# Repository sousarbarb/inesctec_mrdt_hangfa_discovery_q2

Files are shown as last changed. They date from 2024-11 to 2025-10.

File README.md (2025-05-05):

# [Integrating Multimodal Perception into Ground Mobile Robots](https://github.com/sousarbarb/inesctec_mrdt_hangfa_discovery_q2)

Repository contains all the documentation associated with the modifications
made by [INESC TEC](https://www.inesctec.pt/en/) on the
[Hangfa Discovery Q2](https://www.hangfa-europe.com/en/omni-robot/discovery)
mobile platform in order to be compatible with multimodal perception. These
modifications also enable the platform to be integrated in the
[Robot Operating System (ROS)](https://ros.org/), facilitating its usage for
research topics such as perception, localisation and mapping, multi-robot
coordination (when more than one platform is available to the user), Artificial
Intelligence (AI) applied on autonomous mobile robotics, among other topics.

## Setup

### Mobile Platform

Check the
[GitHub Pages website](https://sousarbarb.github.io/inesctec_mrdt_hangfa_discovery_q2/)
for more information on the multimodal modifications made to the original
[Hangfa Discovery Q2](https://www.hangfa-europe.com/en/omni-robot/discovery)
mobile platform.

### Firmware

See [README.md](src/firmware/inesctec_mrdt_discovery_q2_fw/README.md) in the
firmware source folder
([src/firmware/inesctec_mrdt_discovery_q2_fw](src/firmware/inesctec_mrdt_discovery_q2_fw/)).

### Robot Operating System (ROS)

- Drivers:
  - [inesctec_mrdt_drivers_interfaces](src/drivers/inesctec_mrdt_drivers_interfaces)
  - [inesctec_mrdt_hangfa_discovery_q2_driver](src/drivers/inesctec_mrdt_hangfa_discovery_q2_driver)
  - [inesctec_mrdt_omnijoy_driver](src/drivers/inesctec_mrdt_omnijoy_driver)
  - [inesctec_mrdt_serial_channels](src/drivers/inesctec_mrdt_serial_channels)
  - [inesctec_mrdt_serial_port](src/drivers/inesctec_mrdt_serial_port)
  - [livox_ros_driver2](src/drivers/livox_ros_driver2)
    _(may be removed from repo to allow further compatibility with ROS versions)_
  - [rslidar_msg](src/drivers/rslidar_msg)
    _(may be removed from repo to allow further compatibility with ROS versions)_
  - [rslidar_sdk](src/drivers/rslidar_sdk)
    _(may be removed from repo to allow further compatibility with ROS versions)_
- Localization:
  [inesctec_mrdt_localization_odom](src/localization/inesctec_mrdt_localization_odom)
- Launch system:
  [inesctec_mrdt_hangfa_discovery_q2_nav_conf](src/inesctec_mrdt_hangfa_discovery_q2_nav_conf)

**ROS supported versions**
- ROS 1
  - [Ubuntu 20.04.6 LTS](https://releases.ubuntu.com/focal/)
  - [ROS Noetic](https://wiki.ros.org/noetic)
- ROS 2
  - [Ubuntu 20.04.6 LTS](https://releases.ubuntu.com/focal/)
  - [ROS 2 Foxy](https://docs.ros.org/en/foxy/)

_Note:_ remove LiDAR specific packages if you want to compile the original
packages developed in the scope of this work on more recent ROS versions.

**Dependencies**
```sh
sudo apt-get install -y libpcap-dev
sudo apt-get install -y ros-$ROS_DISTRO-joy      \
                        ros-$ROS_DISTRO-pcl-ros  \
                        ros-$ROS_DISTRO-libpointmatcher
```

```sh
# Livox-SDK2
git clone https://github.com/Livox-SDK/Livox-SDK2.git
cd Livox-SDK2/
mkdir build
cd build/
cmake .. && make -j
sudo make install
```

```sh
# yaml-cpp
git clone https://github.com/jbeder/yaml-cpp.git
cd yaml-cpp/
mkdir build
cd build/
cmake .. -DYAML_BUILD_SHARED_LIBS=ON && make -j
sudo make install
```

## Usage

### Repository
```sh
git clone git@github.com:sousarbarb/inesctec_mrdt_hangfa_discovery_q2.git --init --recursive
```

### Build
**ROS 1**
```sh
source /opt/ros/$ROS_DISTRO/setup.bash

cd inesctec_mrdt_hangfa_discovery_q2/src
catkin_init_workspace

cd ..
catkin_make --force-cmake --cmake-args -DCMAKE_BUILD_TYPE=Release

source devel/setup.bash
```

**ROS 2**
```sh
source /opt/ros/$ROS_DISTRO/setup.bash

cd inesctec_mrdt_hangfa_discovery_q2
colcon build --cmake-args -DCMAKE_BUILD_TYPE=Release --event-handlers status+ console_direct+ console_start_end+

source install/setup.bash
```

### Launch

**ROS 1**
```sh
# Robot id
export ROBOT_ID=<id>                # (default: unnamed_robot)
# Configuration
export ROBOT_CONF=<configuration>   # (default: basic)

roslaunch inesctec_mrdt_hangfa_discovery_q2_nav_conf wake_up_dumb_q2.launch
```

**ROS 2**
```sh
# Robot id
export ROBOT_ID=<id>                # (default: unnamed_robot)
# Configuration
export ROBOT_CONF=<configuration>   # (default: basic)

ros2 launch inesctec_mrdt_hangfa_discovery_q2_nav_conf wake_up_dumb_q2.launch.xml
```

## Contributing

Any contributions that you make are greatly appreciated. Please proceed as
follows:
1. Fork the repository
2. Create your feature branch
3. Commit your changes
4. Push to the branch in your repository
5. Open a pull request in the project's original repository

## License

Distributed under the _MIT License_.
See [LICENSE](/LICENSE) for more information.

## References

If you use _inesctec_mrdt_hangfa_discovery_q2_ in a work that leads to a
scientific publication, we would appreciate it if you would kindly cite
_inesctec_mrdt_hangfa_discovery_q2_ in your manuscript.

**Plain Text**

R.B. Sousa, H.M. Sobreira, J.G. Martins, P.G. Costa, M.F. Silva and A.P.
Moreira,
"Integrating Multimodal Perception into Ground Mobile Robots,"
_2025 IEEE International Conference on Autonomous Robot Systems and_
_Competitions (ICARSC2025)_, Madeira, Portugal, 2025, pp. 104-111,
doi: [10.1109/ICARSC65809.2025.10970176](https://doi.org/10.1109/ICARSC65809.2025.10970176)
[[github]](https://github.com/sousarbarb/inesctec_mrdt_hangfa_discovery_q2)
[[preprint]](http://doi.org/10.13140/RG.2.2.29381.15845/1)
[[website]](https://sousarbarb.github.io/inesctec_mrdt_hangfa_discovery_q2/)

**BibTex**

```bibtex
@INPROCEEDINGS{sousa2025icarsc,
  author    = {Ricardo B. Sousa and Héber Miguel Sobreira and João G. Martins and Paulo G. Costa and Manuel F. Silva and António P. Moreira},
  booktitle = {2025 IEEE International Conference on Autonomous Robot Systems and Competitions (ICARSC)},
  title     = {Integrating Multimodal Perception into Ground Mobile Robots},
  year      = {2025},
  volume    = {},
  number    = {},
  pages     = {104--111},
  doi       = {10.1109/ICARSC65809.2025.10970176}}
```

## Contacts

If you have any questions or you want to know more about this work, please
contact one of the following contributors:

- Ricardo B. Sousa
  ([rbs@fe.up.pt](mailto:rbs@fe.up.pt))
  _(Corresponding Author)_
  ([github](https://github.com/sousarbarb/),
  [gitlab](https://gitlab.com/sousarbarb/),
  [gitlab](https://gitlab.inesctec.pt/ricardo.b.sousa),
  [orcid](https://orcid.org/0000-0003-4537-5095),
  [google-scholar](https://scholar.google.pt/citations?user=Bz2FMqYAAAAJ),
  [linkedin](https://www.linkedin.com/in/sousa-ricardob/),
  [youtube](https://www.youtube.com/channel/UCXTR8mMlG0VOC_06PKg5KBQ))
- Héber Miguel Sobreira
  ([heber.m.sobreira@inesctec.pt](mailto:heber.m.sobreira@inesctec.pt))
  ([github](https://github.com/HeberSobreira),
  [gitlab](https://gitlab.inesctec.pt/heber.m.sobreira/),
  [orcid](https://orcid.org/0000-0002-8055-1093),
  [google-scholar](https://scholar.google.pt/citations?user=iNhGcpsAAAAJ))
- João G. Martins
  ([joao.g.martins@inesctec.pt](mailto:joao.g.martins@inesctec.pt))
  ([github](https://github.com/Joao-G-Martins),
  [orcid](https://orcid.org/0000-0002-6567-4802))
- Paulo G. Costa
  ([paco@fe.up.pt](mailto:paco@fe.up.pt))
  ([github](https://github.com/P33a),
  [orcid](https://orcid.org/0000-0002-4846-271X),
  [google-scholar](https://scholar.google.pt/citations?user=7Iz8fKcAAAAJ))
- Manuel F. Silva
  ([mss@isep.ipp.pt](mailto:mss@isep.ipp.pt))
  ([orcid](https://orcid.org/0000-0002-0593-2865),
  [google-scholar](https://scholar.google.pt/citations?user=2EFVZ-AAAAAJ))
- António Paulo Moreira
  ([amoreira@fe.up.pt](mailto:amoreira@fe.up.pt))
  ([orcid](https://orcid.org/0000-0001-8573-3147),
  [google-scholar](https://scholar.google.pt/citations?user=eL0gHLoAAAAJ))

## Institutions

- [INESC TEC - Institute for Systems and Computer Engineering, Technology and Science](https://www.inesctec.pt/en/)
- [Faculty of Engineering, University of Porto (FEUP)](https://sigarra.up.pt/feup/en/)

## Acknowledgements

- [5dpo Robotics Team](https://5dpo.github.io/)
- [Amorins & Silva](https://amorinsesilva.pt/)
- [Hangfa Robotics Europe](https://www.hangfa-europe.com/)
- [LattePanda Team](https://www.lattepanda.com/)

## Funding

This work is co-financed by Component 5 - Capitalization and Business
Innovation, integrated in the Resilience Dimension of the Recovery and
Resilience Plan within the scope of the Recovery and Resilience
Mechanism (MRR) of the European Union (EU), framed in the Next Generation EU,
for the period 2021-2026, within project GreenAuto, with reference 54.

**GreenAuto: Green innovation for the Automotive Industry**

- **Operation Code:** 02/C05-i01.02/2022.PC644867037-00000013
- **Beneficiary:** Peugeot Citröen Automóveis Portugal, S.A.
- **Work Package:** WP10 - Automated logistics for the automotive industry
- **Product, Processes, or Services (PPS):**
  PPS18 - 3D navigation system for mobile robotic equipment
- **Consortium Partners:**
    - [Flowbotic Mobile Systems, Lda](https://www.flowbotic.eu/) _(leader)_
    - [Faculty of Engineering, University of Porto (FEUP)](https://www.up.pt/feup/en/)
    - [INESC TEC - Institute for Systems and Computer Engineering, Technology and Science](https://www.inesctec.pt/en/)
    - [STAR](https://starinstitute.pt/)
    - [Kaizen](https://kaizen.com/pt-pt/)
    - [Institute for Systems and Robotics (ISR)-Coimbra](https://www.isr.uc.pt/)
- **Timeline:** October 2021 - December 2025
- **Duration:** 51 months
- **URL:**
  [https://transparencia.gov.pt/en/fundos-europeus/prr/beneficiarios-projetos/projeto/02/C05-i01.02/2022.PC644867037-00000013/](https://transparencia.gov.pt/en/fundos-europeus/prr/beneficiarios-projetos/projeto/02/C05-i01.02/2022.PC644867037-00000013/)

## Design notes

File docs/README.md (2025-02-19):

# GitHub Pages

Public page of the repository based on GitHub actions through the template
**Material** (https://squidfunk.github.io/mkdocs-material/) from **MkDocs**
(https://www.mkdocs.org/) Markdown-based static site
generation.

## Setup

### GitHub Repository

```sh
mkdir ~/dev
cd ~/dev

git clone git@github.com:sousarbarb/inesctec_mrdt_hangfa_discovery_q2.git
```

### Material for MkDocs

```sh
pip install mkdocs-material
```

## Usage

### Local

```sh
cd ~/dev/inesctec_mrdt_hangfa_discovery_q2

mkdocs serve -a <localhost IP 127.0.0.1>:<PORT>
```

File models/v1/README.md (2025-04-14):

# 3D Models of the Revised Hangfa Discovery Q2 Platform

This folder presents all the 3D models designed for the revised platform in
[AutoDesk Fusion 360](https://www.autodesk.com/products/fusion-360/).
These models include a simplified 3D model for the mechanical platform,
a STEP+F3D file for each 3D-printed PETG component considered in the
revision, as well as a major F3D file that aglomerates all models into a single
project:
- **[hangfa-discovery-q2_mechanical-platform.f3d](hangfa-discovery-q2_mechanical-platform.f3d):**
  original mechanical platform of the
  [Hangfa Discovery Q2](https://www.hangfa-europe.com/en/omni-robot/discovery)
  omnidirectional mobile robot
- **[hangfa-discovery-q2_multimodal-perception-mechanical-integration.f3d](hangfa-discovery-q2_multimodal-perception-mechanical-integration.f3d):**
  major [AutoDesk Fusion 360](https://www.autodesk.com/products/fusion-360/)
  project that aglomerates all 3D models design in the scope of this work into a
  single project file
- **electronics_baseplate\*.\*:** framework to host all the electronics proposed
  in the paper inside the metallic box of the original
  [Hangfa Discovery Q2](https://www.hangfa-europe.com/en/omni-robot/discovery)
  platform
- **battery_xiaomi-powerbank-50W-20000mAh_case\*.\*:** case for the
  Powerbank Xiaomi Mi 50W 20000mAh
- **hangfa-discovery-q2_optitrack_\*.\*:** OptiTrack 3D-printed accessories to
  fixate onto the robot (wheels and top bend metal sheet) in order to track the
  platform's pose with the OptiTrack Motion Capture (MoCap) system
  (compatible with IR-reflective tracking spheres from OptiTrack on M4 screws)
- **sbc_lattepanda-3-delta_case\*.\*:** case for the
  [LattePanda 3 Delta](https://www.lattepanda.com/lattepanda-3-delta)
  Single Board Computer (SBC)
- **sensors-plate_front-support_rgbd-cameras\*.\*:** generic RGBD cameras
  model (see the compatibility further down) as the front support of the top
  bend metal sheet
- **sensors-plate_back-support_wi-fi-antennas\*.\*:** Wi-Fi antennas model as
  the back support of the top bend metal sheet (should increase wireless network
  connectivity)
- **sensors-plate_\<sensor type\>_\<sensor model\>\*.\*:** 3D-printed supports
  to fixate the `<sensor model>` to the top bend metal sheet

Even though the repository is focused on the v1 version of the overhaul revision
of the platform, there was an initial version ([v0](/models/v0/)) that only
focused on adding a 2D laser scanner and no Single Board Computer (SBC). Indeed,
in that version, we assumed the user would use a laptop for testing the
platform.

## 3D Models

### Front Support for RGBD Cameras

**Requirements**

- Intel RealSense D455/455f/456 (M4, 95mm distance between
  two screws horizontal direction,
  _[intel dev](https://dev.intelrealsense.com/docs/intel-realsense-d400-series-product-family-datasheet)_)
- Intel RealSense L515 (M3, 40mm distance between two screws vertical direction,
  _[intel dev](https://dev.intelrealsense.com/docs/lidar-camera-l515-datasheet)_)
- OAK-D and OAD-D Pro Series (M4, 75mm distance between
  two screws horizontal direction - compatibility with VESA mouting holes,
  _[depthai-hardware](https://github.com/luxonis/depthai-hardware)_)

### Generic Support for 3D LiDARs

**Requirements**

- Livox Mid-360 (M3, 65x65mm, 36x48mm rectangular hole pattern,
  _[mid-360 user manual](https://www.livoxtech.com/mid-360/downloads)_)
- Ouster
  |                          | Holes | Dimensions | Distance between Screws | Description | Source |
  | ------------------------ | :---: | :--------: | :---------------------: | ----------- | :----: |
  | OS0 Rev7 w/ Baseplate    | M8    | 110x110mm  | 80mm | square hole pattern | (_[ouster dev](https://static.ouster.dev/sensor-docs/hw_user_manual/hw_common_sections_OS0/os0-overview.html)_) |
  | OS1 Rev7 w/ Baseplate    | M8    | 110x110mm  | 80mm | square hole pattern | (_[ouster dev](https://static.ouster.dev/sensor-docs/hw_user_manual_OS1/hw_common_sections_OS1/os1-overview.html)_) |
  | OSDome Rev7 w/ Baseplate | M8    | 110x110mm  | 80mm | square hole pattern | (_[ouster dev](https://static.ouster.dev/sensor-docs/hw_user_manual_OSDome/hw_common_sections_OSDome/osdome-overview.html)_) |
- RoboSense Helios Series (M3, 99.8mm diameter, 90mm diameter with a triangular hole pattern
  _[helios series user guide](https://www.robosense.ai/en/resources-81)_)
- Velodyne Puck Series / VLP (1/4''-20, 103mm diameter,
  1 center screw with 2x M4 alignment features separated by 88.9mm,
  _[velodyne puck/vlp](https://ouster.com/downloads/velodyne-downloads)_)

## Gallery

**Revised Hangfa Discovery Q2 Platform**

Front-Left Perspective View

Front-Right Perspective View

Front View

Right View

Back View

Left View

**Perspective Views from AutoDesk Fusion 360 on the Revised Platform** _(but still orthographic projection...)_

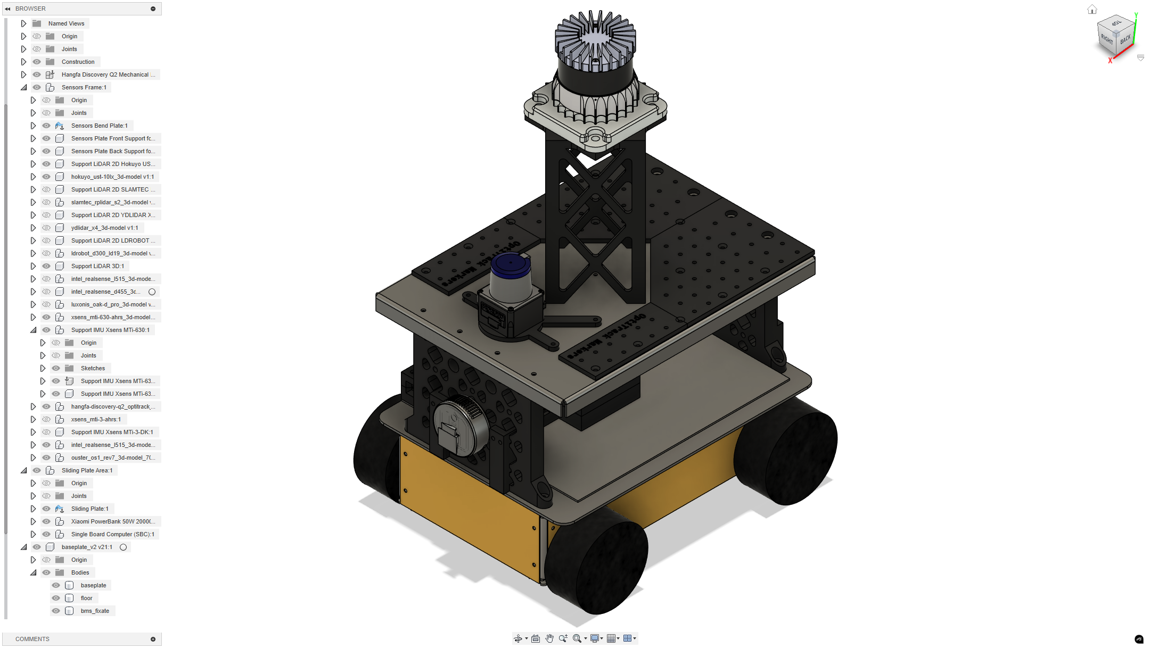
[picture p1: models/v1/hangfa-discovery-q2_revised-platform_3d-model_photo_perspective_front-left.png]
Front-Left Perspective View


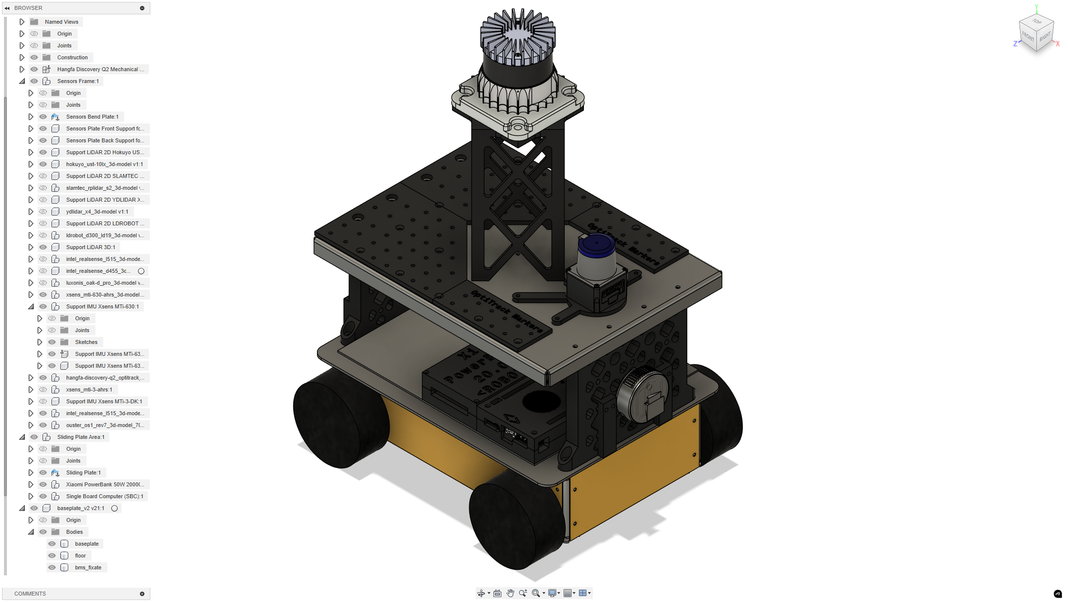
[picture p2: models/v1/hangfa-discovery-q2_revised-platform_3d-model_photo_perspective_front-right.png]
Front-Right Perspective View


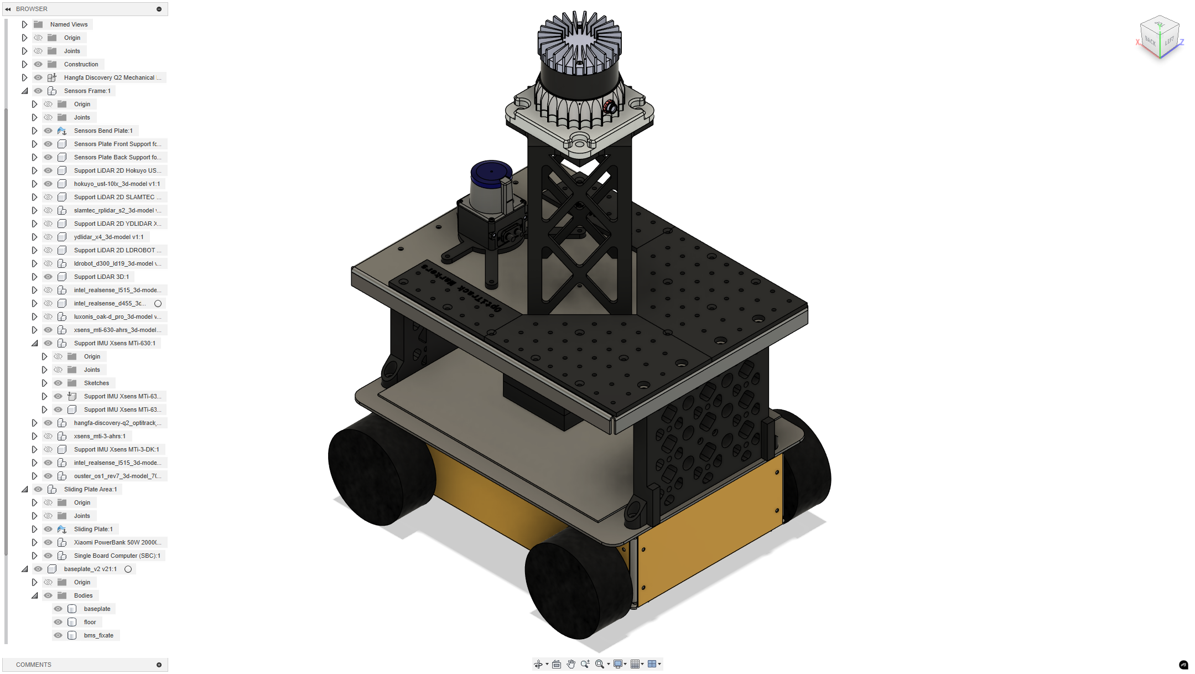
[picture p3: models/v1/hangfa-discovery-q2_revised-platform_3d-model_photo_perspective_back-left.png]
Back-Left Perspective View


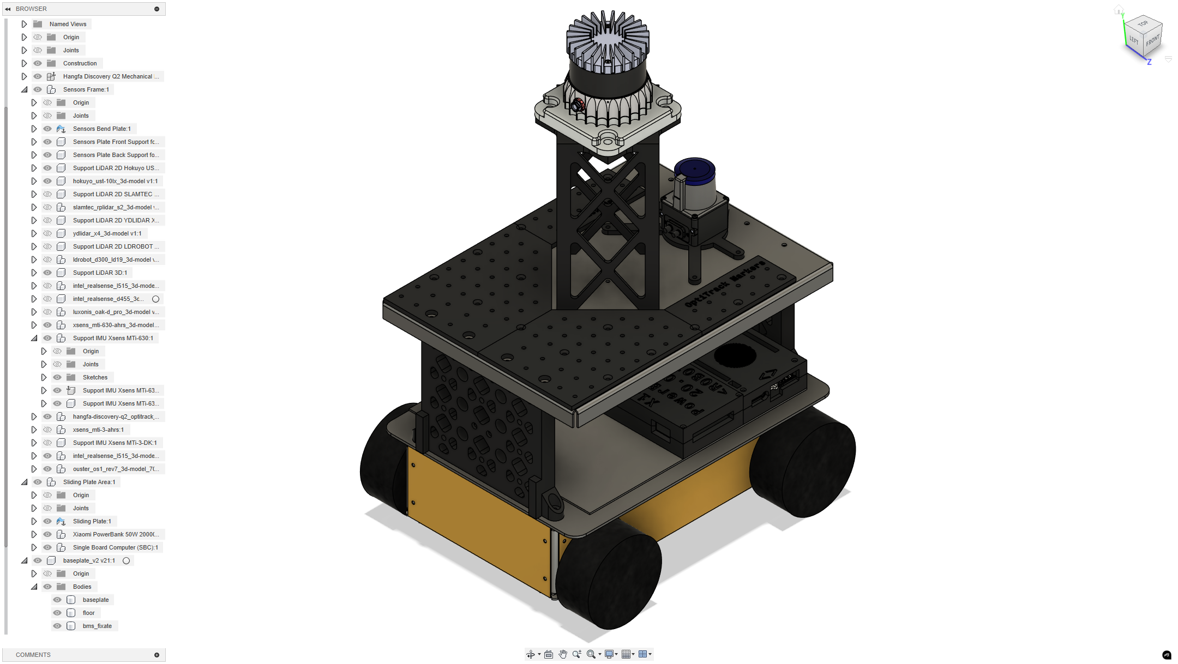
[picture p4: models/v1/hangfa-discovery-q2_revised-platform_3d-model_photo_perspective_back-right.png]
Back-Right Perspective View


**Ortographic Views from AutoDesk Fusion 360 on the Revised Platform**

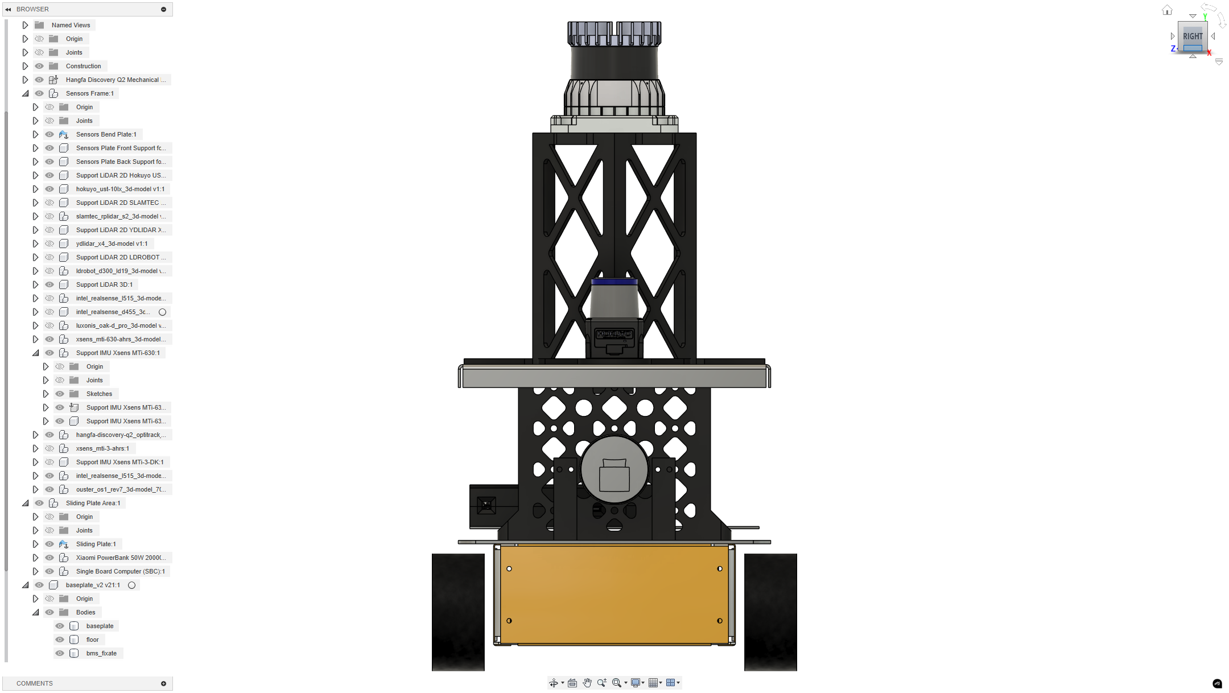
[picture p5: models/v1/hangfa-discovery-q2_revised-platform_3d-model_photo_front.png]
Front Ortographic View


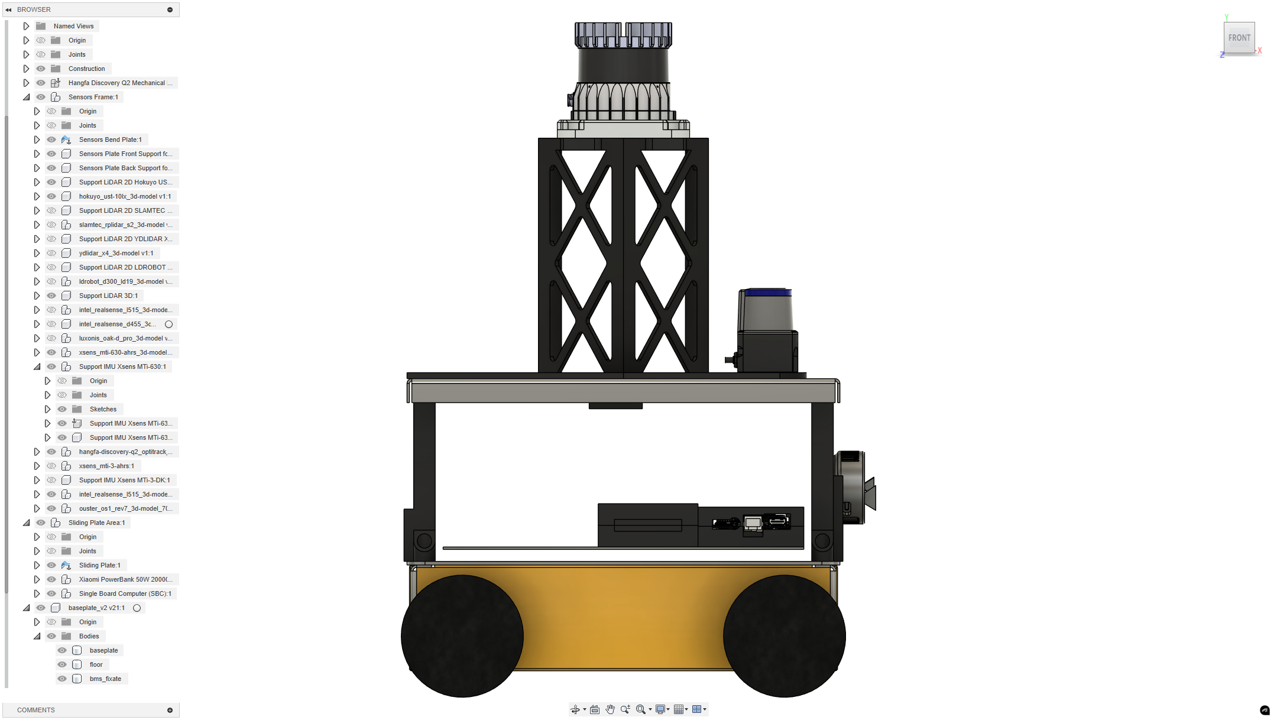
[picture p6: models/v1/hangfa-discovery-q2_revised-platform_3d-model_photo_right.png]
Right Ortographic View


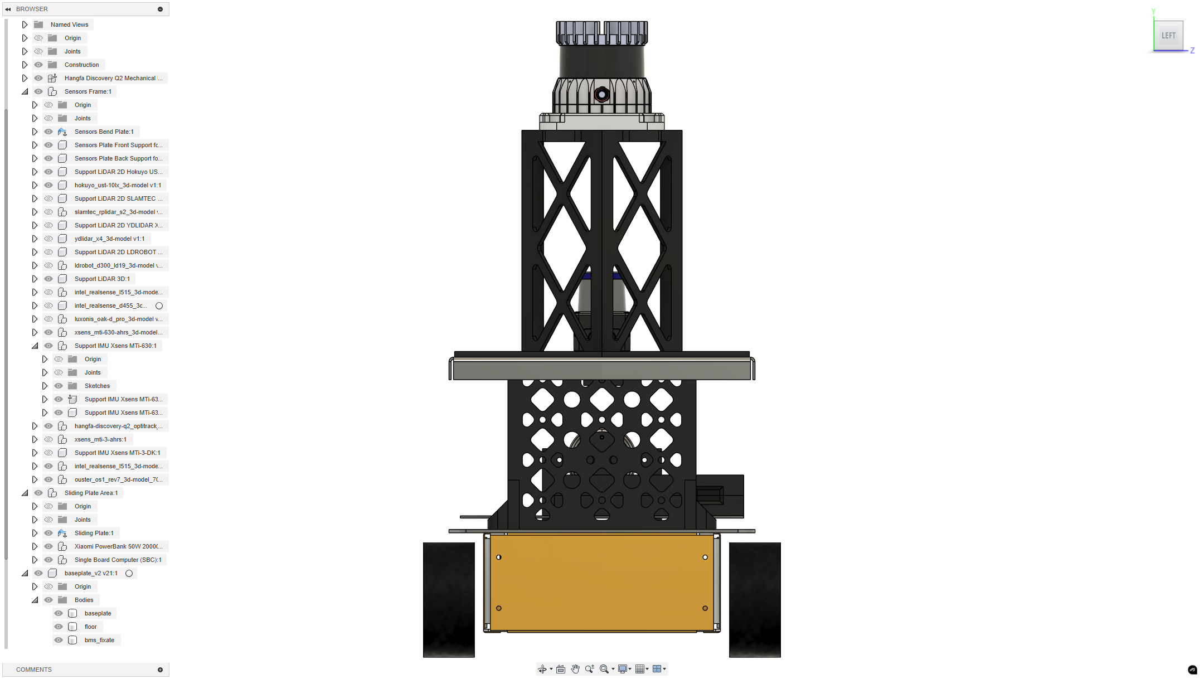
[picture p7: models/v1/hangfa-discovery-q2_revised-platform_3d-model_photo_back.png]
Back Ortographic View


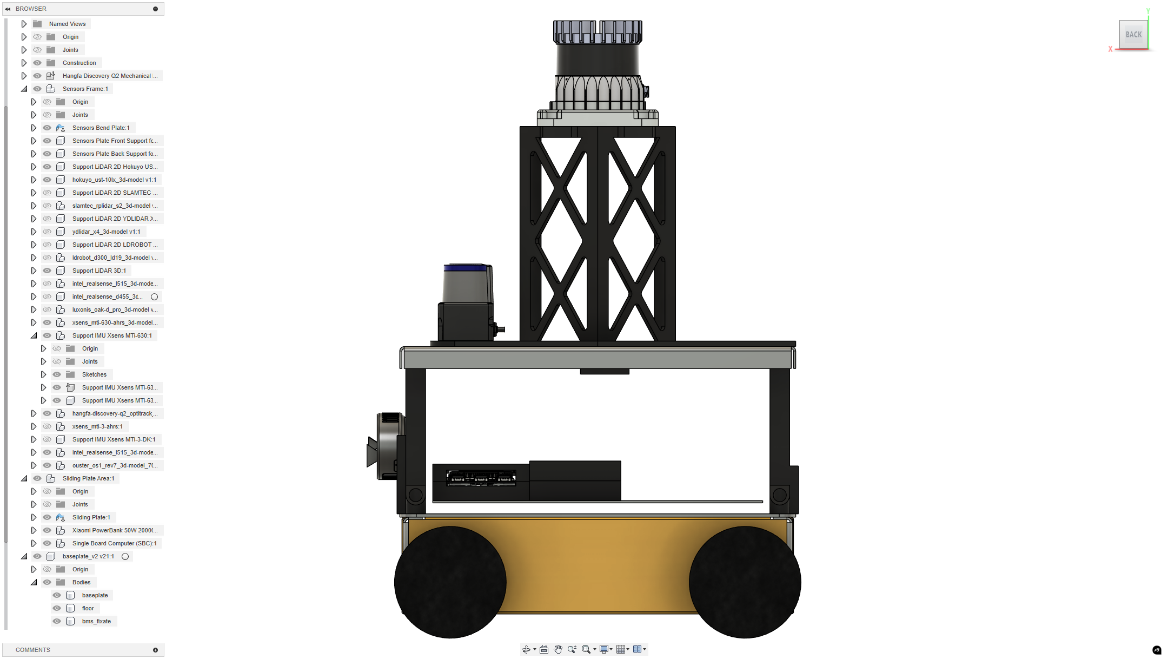
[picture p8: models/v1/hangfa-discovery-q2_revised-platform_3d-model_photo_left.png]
Left Ortographic View


**Miscellaneous...**

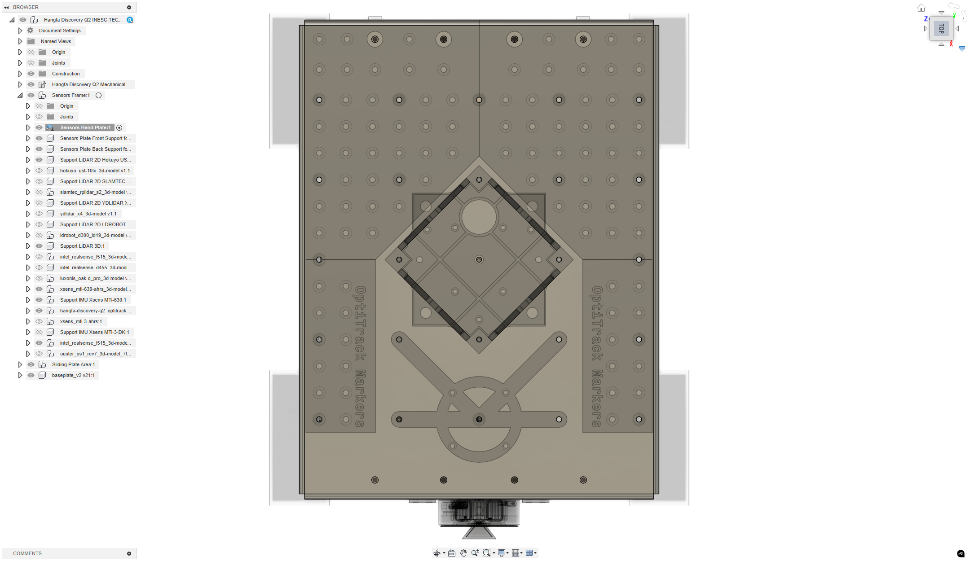
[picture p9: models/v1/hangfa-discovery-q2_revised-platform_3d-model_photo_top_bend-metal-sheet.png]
Bend metal sheet to house 2D/3D sensors


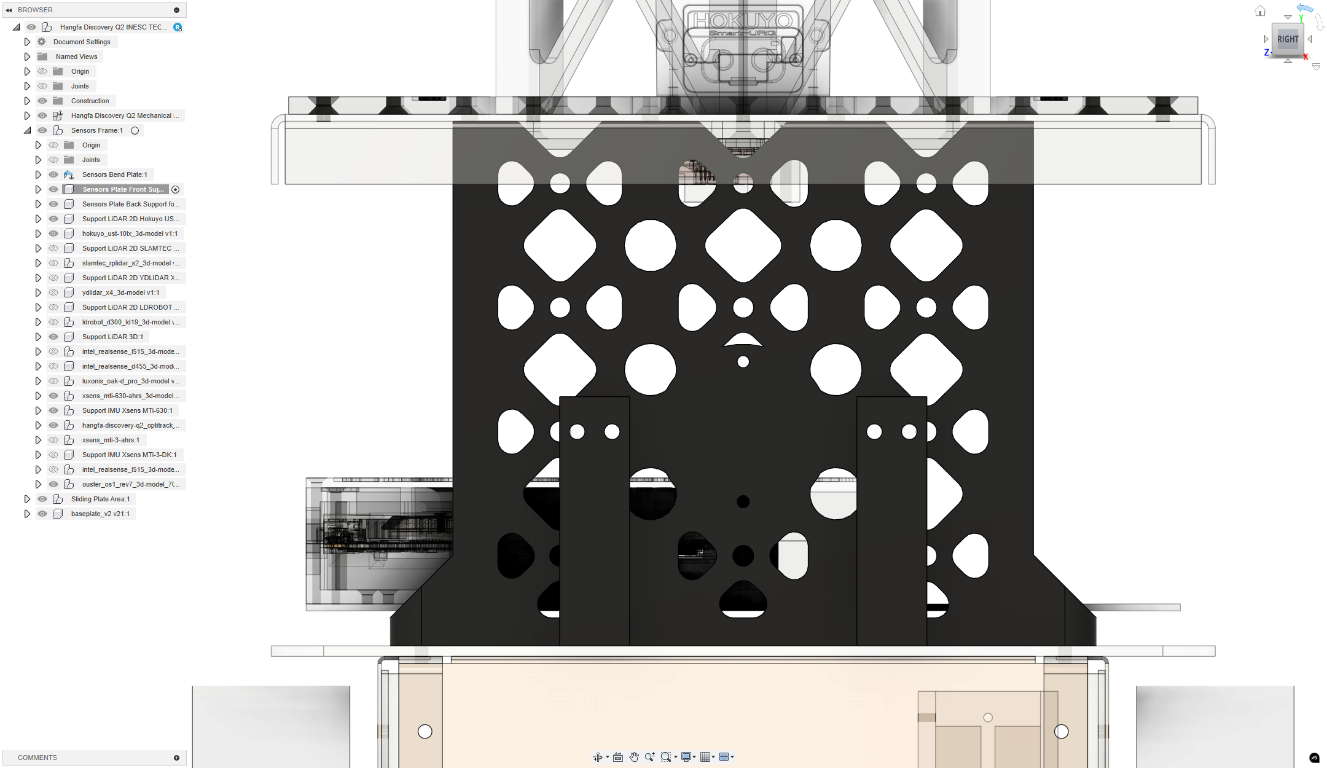
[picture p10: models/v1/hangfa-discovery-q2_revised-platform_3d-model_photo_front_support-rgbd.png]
Front support of the bend metal sheet for RGBD cameras


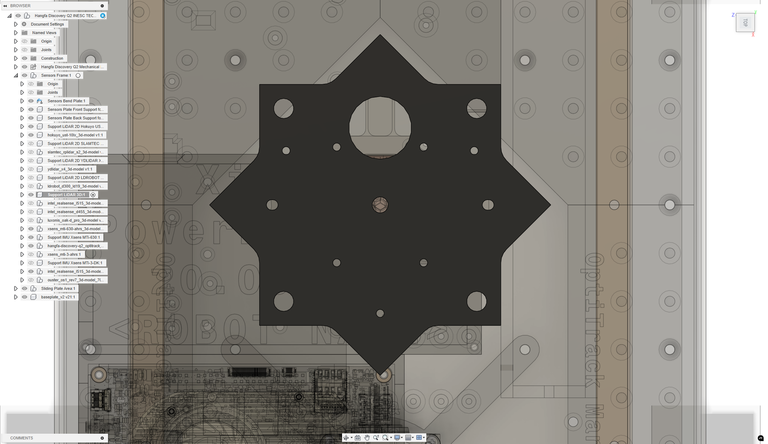
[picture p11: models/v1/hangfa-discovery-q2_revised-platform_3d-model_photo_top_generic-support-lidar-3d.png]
Generic support to fixate on top of the bend metal sheet for 3D LiDARs


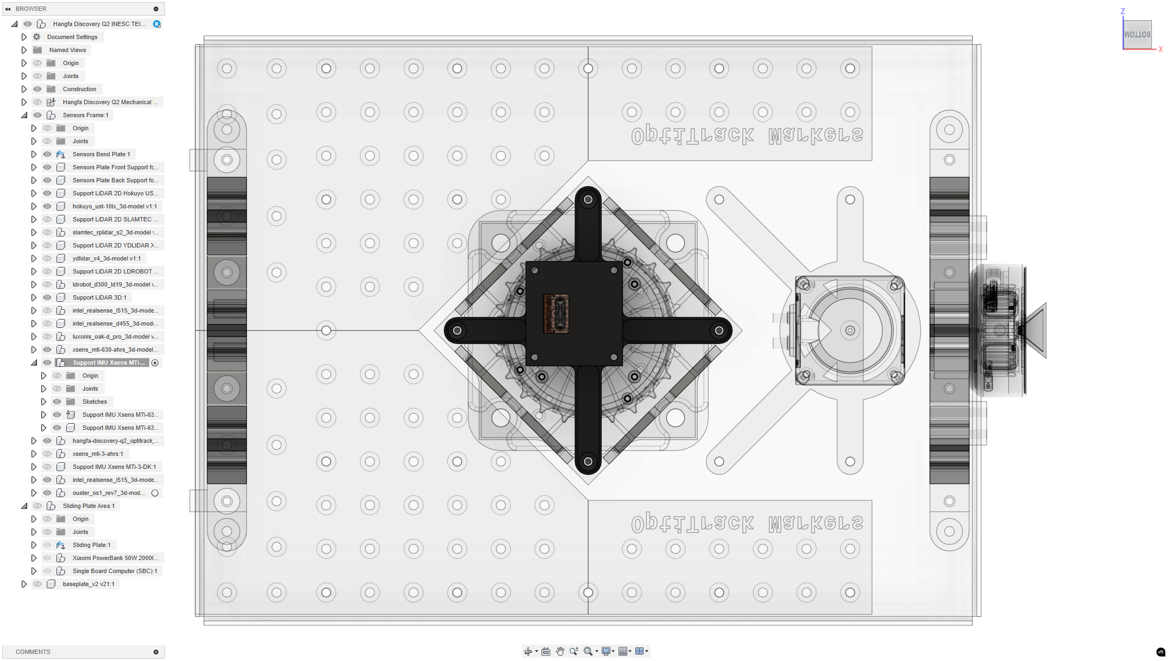
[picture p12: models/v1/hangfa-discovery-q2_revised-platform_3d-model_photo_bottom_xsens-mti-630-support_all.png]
Xsens MTi-630 AHRS support on the bottom of the bend metal sheet - all components visible


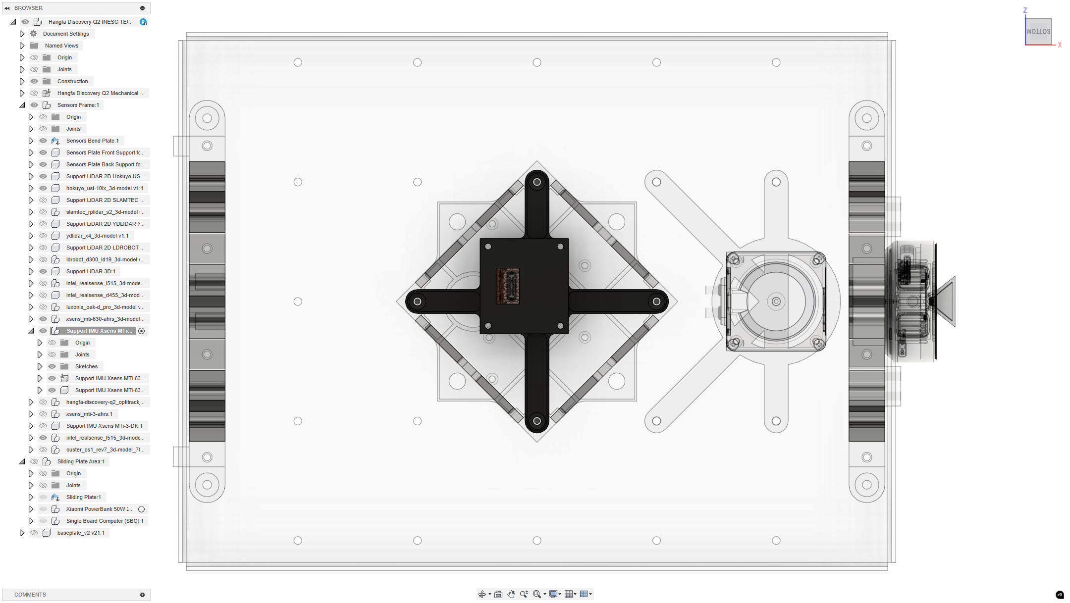
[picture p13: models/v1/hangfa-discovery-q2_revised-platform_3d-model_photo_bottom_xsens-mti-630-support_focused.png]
Xsens MTi-630 AHRS support on the bottom of the bend metal sheet - focused


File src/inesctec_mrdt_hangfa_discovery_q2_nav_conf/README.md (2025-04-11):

# inesctec_mrdt_hangfa_discovery_q2_nav_conf

This repository implements the launch files required to operate the
[Hangfa Discovery Q2](http://www.hangfa.com/EN/robot/DiscoveryQ2.html)
four-wheeled omnidirectional robot, one of the "twin" yellow robots.
The system implemented is based on the INESC TEC Robotics Navigation Stack that
it allows you to have different configurations implemented and selecting just
one based on your environment variables.

**Version 0.3.0**

**With this version, it is possible to do:**

- Basic environment configuration (firmware driver, joystick, wheeled odometry)
- Basic 2D laser scanner configuration (basic + laser 2D) w/ Hokuyo UST-10LX
- Basic 3D LiDAR configuration (basic + lidar 3D) w/ Livox Mid-360

**The next version will add these features:**

- TBD

## Environment Configurations

- `basic`
  - drivers
    - inesctec_mrdt_hangfa_discovery_q2_driver
    - inesctec_mrdt_omnijoy_driver_logif710
  - hmi
    - rviz
  - localization
    - inesctec_mrdt_localization_odom
- `basic_2d`
  - drivers
    - inesctec_mrdt_hangfa_discovery_q2_driver
    - inesctec_mrdt_omnijoy_driver_logif710
    - static_transform_publisher (laser > base_footprint)
    - urg_node
  - hmi
    - rviz
  - localization
    - inesctec_mrdt_localization_odom
  - **Additional configurations:**
    - Network:
      1. Open the Settings > Network
      2. Select the _Hokuyo_ wired interface settings
- `basic_3d`
  - drivers
    - livox_ros_driver2
    - inesctec_mrdt_hangfa_discovery_q2_driver
    - inesctec_mrdt_omnijoy_driver_logif710
    - static_transform_publisher (lidar3d > base_footprint)
  - hmi
    - rviz
  - localization
    - inesctec_mrdt_localization_odom
  - **Additional configurations:**
    - Network:
      1. Open the Settings > Network
      2. Select the _Livox Mid-360_ / _RoboSense Helios_ wired interface
         settings

## ROS

**ROS 1**

- [Ubuntu 20.04.6 LTS](https://releases.ubuntu.com/focal/)
- [ROS Noetic](https://wiki.ros.org/noetic)

**ROS 2**

- [Ubuntu 20.04.6 LTS](https://releases.ubuntu.com/focal/)
- [ROS 2 Foxy](https://docs.ros.org/en/foxy/)

## Usage

### Setup

```sh
# Robot id
export ROBOT_ID=<id>                # (default: unnamed_robot)
# Configuration
export ROBOT_CONF=<configuration>   # (default: basic)
```

### Compilation

**ROS 1**

```sh
# ROS 1 environment setup
source /opt/ros/noetic/setup.bash

# Clone the repository
git clone git@github.com:sousarbarb/inesctec_mrdt_hangfa_discovery_q2.git

# ROS 1 workspace setup
cd inesctec_mrdt_hangfa_discovery_q2/src
catkin_init_workspace

# Build
cd ..
catkin_make --force-cmake -DCMAKE_BUILD_TYPE=Release
# OR catkin_make_isolated (more slow, build and check dependencies individually)
# OR catkin build (requires the Pyhton-based catkin tools)
source devel/setup.bash
```

**ROS 2**

```sh
# ROS 2 environment setup
source /opt/ros/foxy/setup.bash

# Clone the repository
git clone git@github.com:sousarbarb/inesctec_mrdt_hangfa_discovery_q2.git

# Build
cd inesctec_mrdt_hangfa_discovery_q2
colcon build --cmake-args -DCMAKE_BUILD_TYPE=Release --event-handlers summary+ status+ console_cohesion+ console_direct+ console_start_end+ console_stderr+
source install/setup.bash
```

### Launch

**ROS 1**

```sh
roslaunch inesctec_mrdt_hangfa_discovery_q2_nav_conf wake_up_dumb_q2.launch
```

**ROS 2**

```sh
ros2 launch inesctec_mrdt_hangfa_discovery_q2_nav_conf wake_up_dumb_q2.launch.xml
```

## Acknowledgements

- [5dpo Robotics Team](https://5dpo.github.io/)
- [Faculty of Engineering, University of Porto (FEUP)](https://sigarra.up.pt/feup/en/)
- [INESC TEC - Institute for Systems and Computer Engineering, Technology and Science](https://www.inesctec.pt/en/)

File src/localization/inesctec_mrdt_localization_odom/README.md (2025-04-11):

# inesctec_mrdt_localization_odom

This repository implements a data processor for the estimation of the robot pose
based on odometric-only data (e.g., wheeled, laser, visual, and/or inertial
odometry). The ROS package implemented in this repository makes available nodes
that may leverage one and/or multiple sources of odometry data for dead
reckoning pose estimation of the robot.

**Version 1.4.0**

**With this version, it is possible to do:**

- Wheeled odometry (four-wheeled omnidirectional steering geometry)
- Wheeled odometry (differential and three-wheeled omnidirectional steering
  geometries)
- Inverse wheeled odometry
- Enable/disable publication of the tf base_frame_id > odom_frame_id
- Limit the maximum angular speed of the wheels and scale the velocities

**The next version will add these features:**

- Wheeled odometry (tricycle steering geometry)
- Fusion of wheels and inertial odometry data
- Dynamic reconfigure of the nodes parameters
- Additional parameter for covariance (wheeled-inertial odometry fusion)

## ROS

**ROS 1**

- [Ubuntu 20.04.6 LTS](https://releases.ubuntu.com/focal/)
- [ROS Noetic](https://wiki.ros.org/noetic)

**ROS 2**

- [Ubuntu 20.04.6 LTS](https://releases.ubuntu.com/focal/)
- [ROS 2 Foxy](https://docs.ros.org/en/foxy/)

### Dependencies

- [rclcpp](https://index.ros.org/r/rclcpp/) (_ROS 2_)
- [roscpp](https://wiki.ros.org/roscpp/) (_ROS 1_)
- [geometry_msgs](https://index.ros.org/p/geometry_msgs/)
- [nav_msgs](https://index.ros.org/p/nav_msgs/)
- inesctec_mrdt_drivers_interfaces
- [tf2](https://index.ros.org/p/tf2/)
- [tf2_ros](https://index.ros.org/p/tf2_ros/)

### Parameters

- base_frame_id (`std::string = "base_footprint"`): tf frame id of the robot
  base footprint coordinate frame
- odom_frame_id (`std::string = "odom"`): tf frame id of the robot odometry
  coordinate frame
- publish_tf (`bool = true`): enable the publication of the tf
  base_frame_id > odom_frame_id
- invert_tf (`bool = false`): enable the invertion of the tf (odom_frame_id >
  base_frame_id instead of base_frame_id > odom_frame_id)
- w_ref_max_enabled (`bool = false`): enable a maximum angular speed for the
  robot wheels
- w_ref_max (`double`): maximum angular speed of the robot wheels
- steering_geometry: steering geometry of the mobile robot (rad/s)
  (`"diff" | "tricyc" | "omni3" | "omni4"`)
  - Differential drive
    - rob_dist_between_wh (`double`): distance between left-right wheels (m)
    - wh_right_diam (`double`): right wheel diameter (m)
    - wh_right_idx (`size_t`): right wheel index in the
      [mot_enc_array.msg](https://github.com/5dpo/5dpo_ros_interfaces/blob/main/5dpo_ros_interfaces_hw/msg/mot_enc_array.msg)
      (0..1)
    - wh_right_inv (`bool`): invert positive direction of the right
      wheel angular motion
    - wh_left_diam (`double`): left wheel diameter (m)
    - wh_left_idx (`size_t`): left wheel index in the
      [mot_enc_array.msg](https://github.com/5dpo/5dpo_ros_interfaces/blob/main/5dpo_ros_interfaces_hw/msg/mot_enc_array.msg)
      (0..1)
    - wh_left_inv (`bool`): invert positive direction of the left
      wheel angular motion
  - Tricycle
    - TBD
  - Three-wheeled omnidirectional robot
    - rob_dist_center_wh (`double`): distance between the robot geometric center
      and the omnidirectional wheels (m)
    - wh_front_right_diam (`double`): front-right wheel diameter (m)
    - wh_front_right_idx (`size_t`): front-right wheel index in the
      [mot_enc_array.msg](https://github.com/5dpo/5dpo_ros_interfaces/blob/main/5dpo_ros_interfaces_hw/msg/mot_enc_array.msg)
      (0..2)
    - wh_front_right_inv (`bool`): invert positive direction of the front-right
      wheel angular motion
    - wh_front_left_diam (`double`): front-left wheel diameter (m)
    - wh_front_left_idx (`size_t`): front-left wheel index in the
      [mot_enc_array.msg](https://github.com/5dpo/5dpo_ros_interfaces/blob/main/5dpo_ros_interfaces_hw/msg/mot_enc_array.msg)
      (0..2)
    - wh_front_left_inv (`bool`): invert positive direction of the front-left
      wheel angular motion
    - wh_back_diam (`double`): back wheel diameter (m)
    - wh_back_idx (`size_t`): back wheel index in the
      [mot_enc_array.msg](https://github.com/5dpo/5dpo_ros_interfaces/blob/main/5dpo_ros_interfaces_hw/msg/mot_enc_array.msg)
      (0..2)
    - wh_back_inv (`bool`): invert positive direction of the back
      wheel angular motion
  - Four-wheeled omnidirectional robot
    - rob_dist_between_front_back_wh (`double`): distance between front-back
      wheels (m)
    - rob_dist_between_left_right_wh (`double`): distance between left-right
      wheels (m)
    - wh_front_left_diam (`double`): front-left wheel diameter (m)
    - wh_front_left_idx (`size_t`): front-left wheel index in the
      [mot_enc_array.msg](https://github.com/5dpo/5dpo_ros_interfaces/blob/main/5dpo_ros_interfaces_hw/msg/mot_enc_array.msg)
      (0..3)
    - wh_front_left_inv (`bool`): invert positive direction of the front-left
      wheel angular motion
    - wh_front_right_diam (`double`): front-right wheel diameter (m)
    - wh_front_right_idx (`size_t`): front-right wheel index in the
      [mot_enc_array.msg](https://github.com/5dpo/5dpo_ros_interfaces/blob/main/5dpo_ros_interfaces_hw/msg/mot_enc_array.msg)
      (0..3)
    - wh_front_right_inv (`bool`): invert positive direction of the front-right
      wheel angular motion
    - wh_back_left_diam (`double`): back-left wheel diameter (m)
    - wh_back_left_idx (`size_t`): back-left wheel index in the
      [mot_enc_array.msg](https://github.com/5dpo/5dpo_ros_interfaces/blob/main/5dpo_ros_interfaces_hw/msg/mot_enc_array.msg)
      (0..3)
    - wh_back_left_inv (`bool`): invert positive direction of the back-left
      wheel angular motion
    - wh_back_right_diam (`double`): back-right wheel diameter (m)
    - wh_back_right_idx (`size_t`): back-right wheel index in the
      [mot_enc_array.msg](https://github.com/5dpo/5dpo_ros_interfaces/blob/main/5dpo_ros_interfaces_hw/msg/mot_enc_array.msg)
      (0..3)
    - wh_back_right_inv (`bool`): invert positive direction of the back-right
      wheel angular motion

### Subscribes

- cmd_vel (`geometry_msgs::Twist.msg`)
- motors_enc (`inesctec_mrdt_drivers_interfaces::MotEncArray.msg`)

### Publishes

- cmd_vel_ref (`geometry_msgs::Twist.msg`)
- motors_ref (`inesctec_mrdt_drivers_interfaces::MotRefArray.msg`)
- odom (`nav_msgs::Odometry.msg`)
- tf2 (N/A)
  - base_frame_id > odom_frame_id

### Services

None.

### Actions

None.

## Usage

### Compilation

**ROS 1**

```sh
# ROS 1 environment setup
source /opt/ros/noetic/setup.bash

# Clone the repository
git clone git@github.com:sousarbarb/inesctec_mrdt_hangfa_discovery_q2.git

# ROS 1 workspace setup
cd inesctec_mrdt_hangfa_discovery_q2/src
catkin_init_workspace

# Build
cd ..
catkin_make --force-cmake -DCMAKE_BUILD_TYPE=Release
# OR catkin_make_isolated (more slow, build and check dependencies individually)
# OR catkin build (requires the Pyhton-based catkin tools)
source devel/setup.bash
```

**ROS 2**

```sh
# ROS 2 environment setup
source /opt/ros/foxy/setup.bash

# Clone the repository
git clone git@github.com:sousarbarb/inesctec_mrdt_hangfa_discovery_q2.git

# Build
cd inesctec_mrdt_hangfa_discovery_q2
colcon build --cmake-args -DCMAKE_BUILD_TYPE=Release --event-handlers summary+ status+ console_cohesion+ console_direct+ console_start_end+ console_stderr+
source install/setup.bash
```

### Launch

**ROS 1**

```sh
roslaunch inesctec_mrdt_localization_odom inesctec_mrdt_localization_odom_wh.launch
```

**ROS 2**

```sh
ros2 launch inesctec_mrdt_localization_odom inesctec_mrdt_localization_odom_wh.launch.xml
```

## Acknowledgements

- [5dpo Robotics Team](https://5dpo.github.io/)
- [Faculty of Engineering, University of Porto (FEUP)](https://sigarra.up.pt/feup/en/)
- [INESC TEC - Institute for Systems and Computer Engineering, Technology and Science](https://www.inesctec.pt/en/)

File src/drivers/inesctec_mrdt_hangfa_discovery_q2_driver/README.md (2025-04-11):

# inesctec_mrdt_hangfa_discovery_q2_driver

**Version 2.1.1**

This repository implements a driver within a ROS package to communicate with the
firmware present in the Hangfa Q2 Discovery robot. The driver is required
for communicating with the robot and have available all its different functions.

The serial communication is handled by
[Boost.Asio](https://www.boost.org/doc/libs/1_80_0/doc/html/boost_asio.html).
This communication is based on the example `4_callback` provided in the
[serial-port](https://github.com/fedetft/serial-port) GitHub repository.

**With this version, it is possible to do:**

- Communicate with Arduino Mega 2560 using Boost.Asio
  (inesctec_mrdt_serial_port)
- Subscribe motors angular speed reference
- Publish encoders data (encoders + wheels angular speed)
- Read encoders
- Set motors speed
- Reset driver upon reset signal
- Watchdog timer to monitor the motors angular speed reference
- Send serial message to the firmware upon reconnection of the serial port
  communication
- Check automatically (1Hz) the status of the serial port communication

**The next version will add these features:**

No further development is expected for this package.

## ROS

**ROS 1**

- [Ubuntu 20.04.6 LTS](https://releases.ubuntu.com/focal/)
- [ROS Noetic](https://wiki.ros.org/noetic)

**ROS 2**

- [Ubuntu 20.04.6 LTS](https://releases.ubuntu.com/focal/)
- [ROS 2 Foxy](https://docs.ros.org/en/foxy/)

### Dependencies

- [rclcpp](https://index.ros.org/r/rclcpp/) (_ROS 2_)
- [roscpp](https://wiki.ros.org/roscpp/) (_ROS 1_)
- inesctec_mrdt_drivers_interfaces
- inesctec_mrdt_serial_port
- inesctec_mrdt_serial_channels

### Parameters

- encoder_res (`float = 48.0`): resolution of the encoder (ticks/rot)
- gear_reduction (`float = 64.0`): reduction ratio of the transmissions
  (\[gear_reduction:1\])
- serial_port_name (`std::string = "/dev/ttyACM0"`): name of the serial port

### Subscribes

- motors_ref (`inesctec_mrdt_drivers_interfaces::MotRefArray.msg`)

### Publishes

- motors_enc (`inesctec_mrdt_drivers_interfaces::MotEncArray.msg`)

### Services

None.

### Actions

None.

## Usage

### Compilation

**ROS 1**

```sh
# ROS 1 environment setup
source /opt/ros/noetic/setup.bash

# Clone the repository
git clone git@github.com:sousarbarb/inesctec_mrdt_hangfa_discovery_q2.git

# ROS 1 workspace setup
cd inesctec_mrdt_hangfa_discovery_q2/src
catkin_init_workspace

# Build
cd ..
catkin_make --force-cmake -DCMAKE_BUILD_TYPE=Release
# OR catkin_make_isolated (more slow, build and check dependencies individually)
# OR catkin build (requires the Pyhton-based catkin tools)
source devel/setup.bash
```

**ROS 2**

```sh
# ROS 2 environment setup
source /opt/ros/foxy/setup.bash

# Clone the repository
git clone git@github.com:sousarbarb/inesctec_mrdt_hangfa_discovery_q2.git

# Build
cd inesctec_mrdt_hangfa_discovery_q2
colcon build --cmake-args -DCMAKE_BUILD_TYPE=Release --event-handlers summary+ status+ console_cohesion+ console_direct+ console_start_end+ console_stderr+
source install/setup.bash
```

### Launch

**ROS 1**

```sh
roslaunch inesctec_mrdt_hangfa_discovery_q2_driver inesctec_mrdt_hangfa_discovery_q2_driver.launch
```

**ROS 2**

```sh
ros2 launch inesctec_mrdt_hangfa_discovery_q2_driver inesctec_mrdt_hangfa_discovery_q2_driver.launch.xml
```

## Acknowledgements

- [5dpo Robotics Team](https://5dpo.github.io/)
- [Faculty of Engineering, University of Porto (FEUP)](https://sigarra.up.pt/feup/en/)
- [INESC TEC - Institute for Systems and Computer Engineering, Technology and Science](https://www.inesctec.pt/en/)

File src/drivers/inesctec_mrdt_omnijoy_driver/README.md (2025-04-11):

# inesctec_mrdt_omnijoy_driver

**Version 0.1.0**

This repository implements a ROS driver to control an omnidirectional robot
(but also compatible with other steering geometries) with a joystick controller.

**With this version, it is possible to do:**

- Joystick control of a mobile robot
- Dynamic reconfigure of the node parameters

**The next version will add these features:**

No further development is foreseen for this package.

## ROS

**ROS 1**

- [Ubuntu 20.04.6 LTS](https://releases.ubuntu.com/focal/)
- [ROS Noetic](https://wiki.ros.org/noetic)

**ROS 2**

- [Ubuntu 20.04.6 LTS](https://releases.ubuntu.com/focal/)
- [ROS 2 Foxy](https://docs.ros.org/en/foxy/)

### Dependencies

- [rclcpp](https://index.ros.org/r/rclcpp/) (_ROS 2_)
- [roscpp](https://wiki.ros.org/roscpp/) (_ROS 1_)
- [dynamic_reconfigure](https://index.ros.org/p/dynamic_reconfigure/) (_ROS 1_)
- [geometry_msgs](https://index.ros.org/p/geometry_msgs/)
- [joy](https://index.ros.org/p/joy/)
- [sensor_msgs](https://index.ros.org/p/sensor_msgs/)

### Parameters

- axis_linear_x (`int = 1`): index number of x linear axis (`/joy.axes`)
- axis_linear_y (`int = 2`): index number of y linear axis (`/joy.axes`)
- axis_angular (`int = 0`): index number of angular axis (`/joy.axes`)
- axis_deadman (`int = 4`): index number of button for deadman switch
  (`/joy.buttons`)
- axis_turbo (`int = 5`): index number of button for turbo (`/joy.buttons`)
- axis_turbo_up (`int = 6`): index number of button for increasing boost
  (`/joy.buttons`)
- axis_turbo_down (`int = 7`): index number of button for decreasing boost
  (`/joy.buttons`)
- scale_linear (`double = 0.1`): linear scale to normalize (m/s)
- scale_angular (`double = 0.2`): angular scale to normalize (rad/s)
- turbo_scale_linear (`double = 0.2`): use this scale instead of `scale_linear`
  when pressing the turbo button (m/s)
- turbo_max_scale_linear (`double = 0.4`): maximum linear turbo scale (m/s)
- turbo_scale_angular (`double = 0.4`): use this scale instead of
  `scale_angular` when pressing the turbo button (rad/s)
- turbo_max_scale_angular (`double = 0.8`): maximum angular turbo scale (rad/s)

In order to know the index numbers of your controller, go to
[joy](https://wiki.ros.org/joy) documentation, _5. Application_, to see the
options available for those parameters.

### Subscribes

- joy (`sensor_msgs::Joy.msg`)

### Publishes

- cmd_vel (`geometry_msgs::Twist.msg`)

### Services

None.

### Actions

None.

## Usage

### Compilation

**ROS 1**

```sh
# ROS 1 environment setup
source /opt/ros/noetic/setup.bash

# Clone the repository
git clone git@github.com:sousarbarb/inesctec_mrdt_hangfa_discovery_q2.git

# ROS 1 workspace setup
cd inesctec_mrdt_hangfa_discovery_q2/src
catkin_init_workspace

# Build
cd ..
catkin_make --force-cmake -DCMAKE_BUILD_TYPE=Release
# OR catkin_make_isolated (more slow, build and check dependencies individually)
# OR catkin build (requires the Pyhton-based catkin tools)
source devel/setup.bash
```

**ROS 2**

```sh
# ROS 2 environment setup
source /opt/ros/foxy/setup.bash

# Clone the repository
git clone git@github.com:sousarbarb/inesctec_mrdt_hangfa_discovery_q2.git

# Build
cd inesctec_mrdt_hangfa_discovery_q2
colcon build --cmake-args -DCMAKE_BUILD_TYPE=Release --event-handlers summary+ status+ console_cohesion+ console_direct+ console_start_end+ console_stderr+
source install/setup.bash
```

### Launch

**ROS 1**

```sh
roslaunch inesctec_mrdt_omnijoy_driver inesctec_mrdt_omnijoy_driver_logif710.launch
```

**ROS 2**

```sh
ros2 launch inesctec_mrdt_omnijoy_driver inesctec_mrdt_omnijoy_driver_logif710.launch.xml
```

## Acknowledgements

- [@fedetft](https://github.com/fedetft)
- [5dpo Robotics Team](https://5dpo.github.io/)
- [Faculty of Engineering, University of Porto (FEUP)](https://sigarra.up.pt/feup/en/)
- [INESC TEC - Institute for Systems and Computer Engineering, Technology and Science](https://www.inesctec.pt/en/)

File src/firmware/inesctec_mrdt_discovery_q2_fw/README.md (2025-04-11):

# inesctec_mrdt_discovery_q2_fw

This repository implements the firmware relative to the modified
Hangfa Discovery Q2 four-wheeled omnidirectional robotic platform.

**Version 2.2.0**

**With this version, it is possible to do:**

- Serial communication using the library channels
- Read encoders channel A and B for wheeled odometry
- Motors angular speed control with a generic PID controller
- Motors PWM control
  ([TimerOne](https://github.com/PaulStoffregen/TimerOne) and
  [TimerThree](https://github.com/PaulStoffregen/TimerThree) PWM)
- Watchdog timer to disable the motors if the PC does not send anything for a
  certain time
- Limitation on the PWM change

**The next version will add these features:**

- Tune the PID controllers for angular speed control of the motors

**Bugs identified in the current version:**

- None

## Hardware

- Hangfa Discovery Q2 Platform
- Faulhaber DC Motor 2342 OEM
  ([datasheet [not possible to validate this link...]](https://www.faulhaber.com/fileadmin/Import/Media/EN_2342_CR_DFF.pdf))
  - 3K3 Ohms Resistors (pull-up resistor for the encoders channels)
- Arduino Mega 2560 Rev3
- Arduino Mega Proto Shield Rev3
  - IDC Socket 6Way
    ([store](https://mauser.pt/catalog/product_info.php?products_id=011-0827))
  - IDC Header Straight 6Way
    ([store](https://mauser.pt/catalog/product_info.php?products_id=011-0800))
  - 8-pin stackable header (Arduino Compatible)
    ([store](https://opencircuit.nl/product/female-header-stackable-8-pin-10-stuks))
  - 10-pin stackable header (Arduino Compatible)
    ([store](https://opencircuit.nl/product/female-header-stackable-10-pin-10-stuks))
  - 2x18-pin stackable header (Arduino Compatible)
    ([store](https://opencircuit.nl/product/female-header-stackable-2x18-pin-2-stuks))
- Cytron 13A, 5-30V Single DC Motor Controller
  - KK shell connector 3Way 2.54mm (Molex 5051 Housing)
    ([store](https://mauser.pt/catalog/product_info.php?products_id=011-1319))
  - Terminals KK shell connector 3Way 2.54mm
    ([store](https://mauser.pt/catalog/product_info.php?products_id=011-3065))
- Li-Ion 18650 BMS Charger PCB, 3S 12.6V 20A
- Tattu 11.1V 15C 3S 10000mAh Lipo Battery Pack

## Serial Communication (channels)

**Robot > PC**

- `[g]`: encoders total count of motor 0 (ticks)
- `[h]`: encoders total count of motor 1 (ticks)
- `[i]`: encoders total count of motor 2 (ticks)
- `[j]`: encoders total count of motor 3 (ticks)
- `[k]`: interval time between control cycles (us)
- `[r]`: reset signal

**PC > Robot**

- `[G]`: reference angular speed of motor 0 (rad/s)
- `[H]`: reference angular speed of motor 1 (rad/s)
- `[I]`: reference angular speed of motor 2 (rad/s)
- `[J]`: reference angular speed of motor 3 (rad/s)
- `[K]`: PWM value of motors
  - `(value >> 24) & 0x03`: motor index (0..3)
  - `value & 0xFFFF`: PWM value (0..`kMotPWMmax`)

## Usage

**Requirements**

- PlatformIO extension for VS Code

### Compilation

**Visual Studio Code**

1. Clone the repository
    ```sh
    git clone git@github.com:sousarbarb/inesctec_mrdt_hangfa_discovery_q2.git
    cd inesctec_mrdt_hangfa_discovery_q2/src/firmware/inesctec_mrdt_discovery_q2_fw
    code .
    ```
2. Compile the project using the PlatformIO extension in VS Code
   (PlatformIO on left-side navigation bar > Project Tasks > Build)

### Run

1. Open the PlatformIO project in the Visual Studio Code
2. Upload the project using the PlatformIO extension in VS Code
   (PlatformIO on left-side navigation bar > Project Tasks > Upload)

## Acknowledgements

- [5dpo Robotics Team](https://5dpo.github.io/)
- [Faculty of Engineering, University of Porto (FEUP)](https://sigarra.up.pt/feup/en/)
- [INESC TEC - Institute for Systems and Computer Engineering, Technology and Science](https://www.inesctec.pt/en/)

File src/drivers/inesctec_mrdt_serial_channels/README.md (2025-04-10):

# inesctec_mrdt_serial_channels

**Version 1.0**

This folder contains a ROS package that defines a library to communicate with
another devices such as Arduinos (Uno, Mega, etc). The communication protocol is
based on the _channels_ library developed by professor Paulo Costa. The current
version is an improvement over the one developed by Héber Miguel Sobreira
(https://gitlab.inesctec.pt/heber.m.sobreira/serial_communication_channels.git)
in the way that allows channels between 'g'-'z' and 'G'-'Z'. An important note
is that you must check if on the Arduino side the hexdecimals characters
correspond to the ones consider in this package: '0'..'9','A'..'F'.

Lastly, it is possible to use the same library on the Arduino (example provided
by Héber Miguel Sobreira - please contact him through email
[heber.m.sobreira@inesctec.pt](mailto:heber.m.sobreira@inesctec.pt)
for further informations on this matter).
However, this implementation uses reallocs of memory. Even though it is only
when the Arduino turns on, I did not think that this approach would be the
correct one due to Arduinos do not have a proper memory management system. So,
the one used on the Arduino is the same one developed by professor Paulo Costa.
**Main disadvantage:** the Arduino only interprets fixed-size packets
(specifically, 4 bytes of data: `float`, `uint32_t` or `int32_t`).

**With this version, it is possible to:**

- Send data of the following types: `float`, `uint32_t` or `int32_t`
  (limited because of the implementation on the Arduino side)
- 40 different channels with different functions associated with each one
  ('g'-'z' and 'G'-'Z')

**The next version will add these features:**

- Binary write and read (compression that allows to reduce from 8 to 4 bytes of
  data on certain data types)

## ROS

**ROS 1**

- [Ubuntu 20.04.6 LTS](https://releases.ubuntu.com/focal/)
- [ROS Noetic](https://wiki.ros.org/noetic)

**ROS 2**

- [Ubuntu 20.04.6 LTS](https://releases.ubuntu.com/focal/)
- [ROS 2 Foxy](https://docs.ros.org/en/foxy/)

## Communication Protocol

- `[CHANNEL]` + `[DATA]` + `\0`
- `[CHANNEL]`: 'g'-'z', 'G'-'Z'
- `[DATA]`: characters that represent a value in hexadecimal

## Acknowledgements

- [5dpo Robotics Team](https://5dpo.github.io/)
- [Faculty of Engineering, University of Porto (FEUP)](https://sigarra.up.pt/feup/en/)
- [INESC TEC - Institute for Systems and Computer Engineering, Technology and Science](https://www.inesctec.pt/en/)
- [Héber Miguel Sobreira](https://gitlab.inesctec.pt/heber.m.sobreira/)
- [Paulo G. Costa](https://github.com/P33a)

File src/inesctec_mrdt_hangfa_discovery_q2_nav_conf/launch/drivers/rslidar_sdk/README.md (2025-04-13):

# [RoboSense RS-Helios 5515](https://www.robosense.ai/en/rslidar/RS-Helios)

## Specifications

| Description | Specification |
| :--- | :---: |
| #beams | 32 |
| Blind spot | 0.2m |
| Frame rate | 10 / 20Hz |
| Rotation speed | 600rpm @ 10Hz, 1200rpm @ 20Hz |
| HFOV | 360º |
| VFOV | 70º (-55º..+15º) |
| Horizontal resolution | 0.2º @ 10Hz, 0.4º @ 20Hz |
| Vertical resolution | up to 1.33º (not uniform) |
| Operating Voltage | 9..32V |
| Power consumption | 12W (typical), 20W (peak) |

## Setup

1. Power up the sensor
2. Connect an Ethernet cable to your PC
3. Configure a local network:
   - Manual
   - Address: 192.168.1.102
   - Netmask: 255.255.255.0
4. Validate the sensor configuration with the web browser: http://192.168.1.200/
   - **Return Mode:** due to beam divergence, multiple laser returns may appear
     from any single laser shot
     - Strongest
     - Last
     - First
     - Dual: details enhance, twice the volume of data versus single return mode
       - Sensor records both returns only when distance between two objects is
         greater than 1m
   - **Phase Lock:** when multiple lasers are used at the same time, with a PPS
     pulse signal; indicates the firing angle of the sensor's laser at the time
     of the rising edge of the PPS signal
   - **Reflectivity Enhance:** noise filter

## ROS

### Version

- ROS1
- ROS2

### Setup

**foxy**

1. Install a ROS 2 full desktop version
2. Download and install dependencies
   ```sh
   sudo apt-get install -y  libpcap-dev
   ```
3. Clone and configure the SDK repository
   (https://github.com/RoboSense-LiDAR/rslidar_sdk)
   ```sh
   # ROS 2
   source /opt/ros/foxy/setup.bash
   mkdir -p ~/ros2_ws/src
   cd ~/ros2_ws/src

   git clone git@github.com:sousarbarb/rslidar_sdk.git
   git clone git@github.com:sousarbarb/rslidar_msg.git

   cd rslidar_sdk
   git submodule init
   git submodule update --recursive

   cp package_ros2.xml package.xml
   nano CMakeLists.txt    # change CATKIN to COLCON

   # Build
   cd ~/ros2_ws
   colcon build
   source install/setup.bash
   ```
   - **Note:** a fork was made from the original SDK to support putting the
     config file in another folder

### Launch

```sh
roslaunch inesctec_mrdt_hangfa_discovery_q2_nav_conf run_rslidar_sdk.launch.xml
```

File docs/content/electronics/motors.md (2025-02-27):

# Motors

| Description | Value |
| :--- | :---: |
| Model | Faulhaber 2342 OEM DC motor |
| Voltage (Rated) | 12V |
| Current (Rated) | 1.1A |
| Output Power (Rated) | 11W |
| Speed (Rated) | 5800rpm |
| Speed (No-load) | 6800rpm |
| Encoders | 5V, 2 channels, 12CPR |
| Fixation Type | outer body bearing block bears the wheel in axial and radial loads |

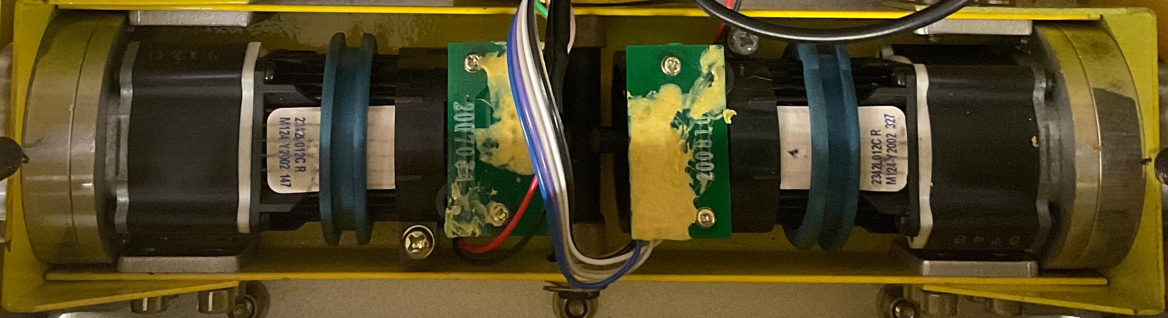
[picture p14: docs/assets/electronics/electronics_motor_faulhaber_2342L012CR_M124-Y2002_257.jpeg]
Faulhaber 2342 OEM DC motor on Discovery Q2 Platform


## Drivers

- **Goal:** control the DC motors of the original
  [Hangfa Discovery Q2](https://www.hangfa-europe.com/en/omni-robot/discovery)
  mobile platform
- **Model:** Cytron 13A 5-30V Single DC Motor Driver
- Voltage range 5-30V compatible with the Faulhaber 2342 OEM DC motor (12V)
- Maximum continuous current of 13A and peak motor current of 30A should be
  compatible with the Faulhaber 2342 OEM DC motor (rated at 1.1A, 11W)
- Single PWM signal for speed control with a digital direction pin to set the
  direction of the motor speed
- 3.3V and 5V logic level input compatible with the Arduino Mega 2560
  microcontroller

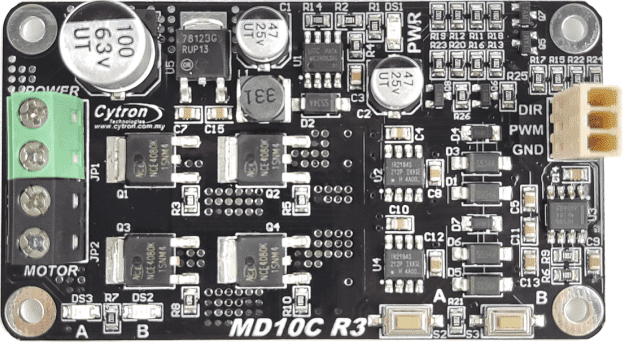
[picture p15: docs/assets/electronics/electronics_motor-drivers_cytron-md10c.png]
Cytron 13A 5-30V Single DC Motor Driver


## Encoders

- **Goal:** 5V, 2 channels, 12CPR encoders present on the Faulhaber 2342 OEM DC
  motors (green PCB board on top of the motors) generate quadrature signals for
  the microcontroller to read the angular speed of the motors
- **Requirement:** upon experimental test, 3.3 kΩ pull-up resistors are soldered
  to the channels A and B inputs of the four encoders on the microcontroller's
  proto shield to reduce signal noise and improve the quadrature between
  channels A and B

!!! Warning

    The cables on the encoders of the original
    [Hangfa Discovery Q2](https://www.hangfa-europe.com/en/omni-robot/discovery)
    mobile platform seem to not be correctly soldered into the encorder's green
    board. This flaw may lead to incorrect encoders reading. As a result, you
    probably are more safe if you resolder all the cables in the encoders.

!!! Tip

    The yellow stuff on the encoder's green board comes out with heat (e.g., use
    a heat gun carefully with the help of a tool to remove the yellow stuff in
    order to be able to resolder the cables).

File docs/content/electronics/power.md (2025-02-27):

# Power

## Battery

- **Goal:** power all the electronics related to the robot's base platform
  (including motors, motor drivers, external devices of the user that may
  require DC power)
- **Model:** Tattu 10000mAh 11.1V 15C 3S LiPo Battery
- 11.1V makes it compatible to power the Faulhaber 2342 OEM DC motors (12V)
- 11.1V is also compatible to power the Arduino Mega 2560 (7-12V recommended,
  6-20V limit), even though the microcontroller can be powered directly from the
  USB connection

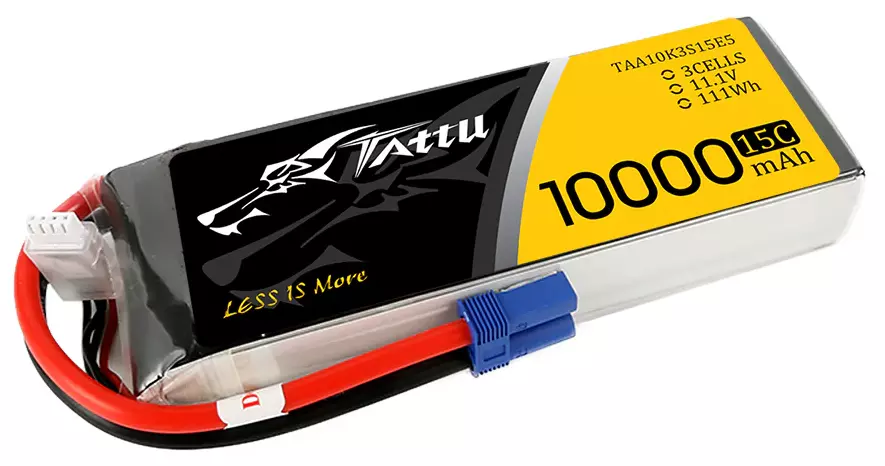
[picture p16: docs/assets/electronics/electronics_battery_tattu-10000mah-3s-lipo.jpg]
Tattu 10000mAh 11.1V 15C 3S LiPo Battery


## Battery Management System (BMS)

- **Goal:** balance the voltage of the battery cells both when discharging and
  upon charging
- **Model:** 18650 BMS Charger 3S 12.6V 20A Rev. 2.0
- Compatible with 3S (three cells in series) batteries
- Compatible with the maximum voltage of each LiPo cell (4.2V)

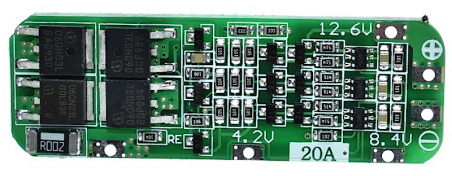
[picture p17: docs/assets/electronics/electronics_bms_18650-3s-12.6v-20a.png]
18650 BMS Charger 3S 12.6V 20A Rev. 2.0


## DC/DC Buck-Boost Converter

- **Goal:** provide a regulated and adjustable DC power output for external
  devices (e.g., Ethernet switch, 3D LiDARs)
- **Model:** DC 5-30V to 1.25-30V 8A Buck Boost Converter
- Input voltage compatible with the output voltage of the LiPo battery
- Output voltage compatible with common voltage values such as 5V / 12V / 24V

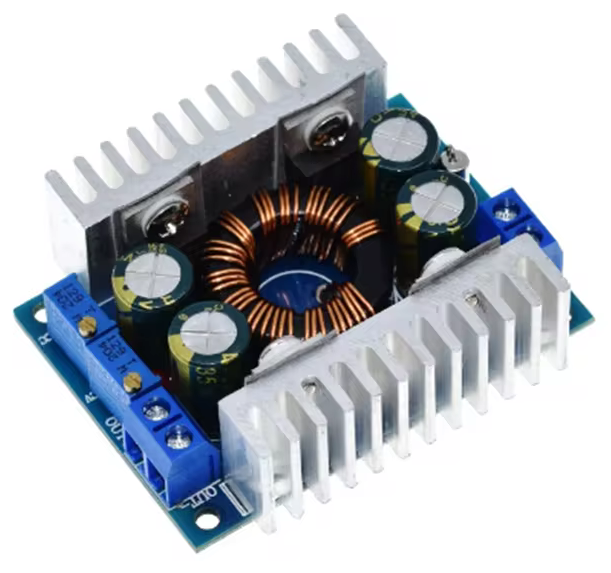
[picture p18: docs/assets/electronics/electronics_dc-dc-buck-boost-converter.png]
DC 5-30V to 1.25-30V 8A Buck Boost Converter


## Charging

**Hangfa Discovery Q2**

- **A:** charging connector
- **B:** 20A power fuse for electrical protection
- **C:** ON/OFF switch

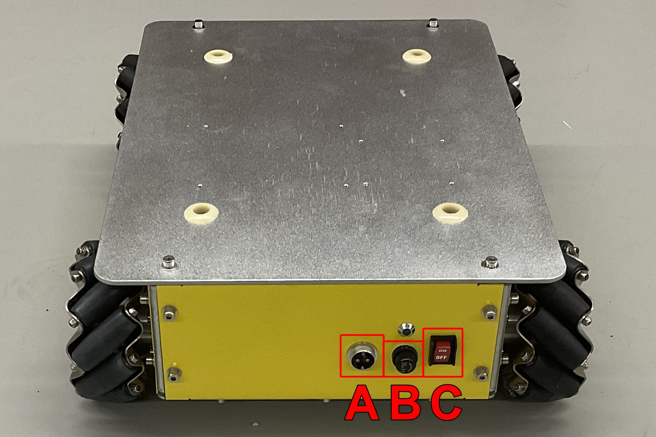
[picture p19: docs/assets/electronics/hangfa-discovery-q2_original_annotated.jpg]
Front View of the Hangfa Discovery Q2 Platform


### Original Charger

**Model:** KXD-126300 Li-ion charger, 100~240VAC input, 12.6VDC @ 3.0A output

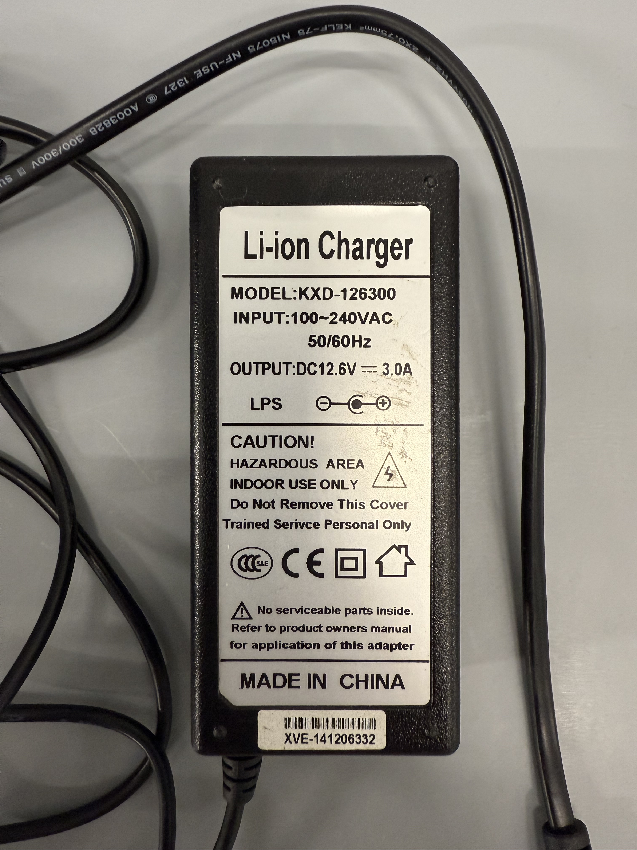
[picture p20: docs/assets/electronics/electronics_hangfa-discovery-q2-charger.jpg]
KXD-126300 Li-ion charger, 100~240VAC input, 12.6VDC @ 3.0A output


!!! Warning

    The original charger that comes with the platform may not be the
    most suitable for charging the LiPo battery. Even if the charger
    indicator turns green, it does not necessarily mean that charging
    has stopped, which could lead to overcharging and potentially
    swollen batteries.

1. Turn OFF the Discovery Q2 platform
2. Connect the charger to AC power (LED on the charger should turn green)
3. Connect the charger output plug to the Discovery Q2 platform
    - If the LED on the charger turns red, it is charging the platform
    - Otherwise, the battery is fully charged
4. Disconnect the charger from the platform when the battery is fully charged

### LiPo Charger

- **Model:** LiPo Battery Charger LBC-011 (or any other charger specific for
  LiPo batteries)
    - [iMAX B6AC User Manual](../../assets/electronics/battery-charger_imaxb6ac_user-manual.pdf)

LiPo Battery Charger LBC-011

1. Turn OFF the Discovery Q2 platform
2. Connect the charger to AC power (charger screen should turn on)
3. Select the **CHARGE** mode (use the buttons
   **:octicons-triangle-left-24: Status :octicons-triangle-right-24:** to
   navigate through the available modes)
4. If the charger is not configure for **LiPo** batteries
    1. Press (just one click!) **Batt. Type** button
    2. Select **PROGRAM SELECT LiPo BATT** (use the buttons
   **:octicons-triangle-left-24: Status :octicons-triangle-right-24:** to
   navigate through the available programs and settings)
    3. Press (just one click!) **Enter**
5. If the charger is not configure for **3.0A 11.1V (3S)** when in
   **CHARGE** mode
    1. Press (just one click!) **Enter** button
    2. Use the buttons
       **:octicons-triangle-left-24: Status :octicons-triangle-right-24:** to
       adjust the charging current to **3.0A**
    3. Press (just one click!) **Enter** button
    4. Use the buttons
       **:octicons-triangle-left-24: Status :octicons-triangle-right-24:** to
       select the **11.1V (3S)** battery configuration
    3. Press (just one click!) **Enter** button
6. Connect the charger output plug to the Discovery Q2 platform
7. Long press on the **Start** button to start the charging
8. Press (just one click!) **Enter** button to confirm the **11.1V (3S)**
   battery configuration
9. Charger should terminate automatically the charging when the battery is fully
   charged
10. Press **Stop** button to stop the charging
11. Disconnect the charger from the platform when the battery is fully charged

See the [User Manual](../../assets/electronics/battery-charger_imaxb6ac_user-manual.pdf)
of the charger for more information on its configurations.

## Power Budget

In terms of power budget, the modified platform considers different sensor
configurations in terms of compatibility. As a result, the following power
budgets are only examples for possible configurations that you may have in your
modified platform.

### 2D Navigation (Low-cost 2D Lasers)

**Total Power Budget handled by the LiPo Battery**

| Source | Voltage (V) | Current (A) | Power (W) |
| :--- | :---: | :---: | :---: |
| 4 x Faulhaber 2342 OEM DC motors | 12V | 4 x 1.1A | 4 x 11W |
| 1 x Arduino Mega 2560 | 12V | 0.750A | - |

- **Power Consumption:** 53W _(estimated)_
- **Current Consumption:** 4.8A @ 11.1VDC
- **Autonomy:** > 2h05min

!!! Note

    - Faulhaber 2342 OEM DC motors 1.1A and 11W are the rated current and power,
      respectively (typically, given that robot carries a low load, should be
      much less than 1.1A continuously)
    - Arduino Mega 2560 current consumption was considered the maximum one
      supported by the SPX1117M3-L-5-0/TR DC Regulator for the PWRIN power input
      (750mA)
    - LD19 | RPLIDAR C1 | RPLIDAR S2 | YDLIDAR X4: all connect to the computing
      unit through USB connection, and the computing unit is powered by an
      independent power source / power bank

**Total Power Budget handled by a 20000mAh 50W Power Bank for the Computing Unit**

| Source | Voltage (V) | Current (A) | Power (W) |
| :--- | :---: | :---: | :---: |
| 1 x LattePanda 3 Delta | 15V | 3A | - |

- **Power Consumption:** 45W _(estimated)_
- **Current Consumption:** 3A @ 15VDC
- **Autonomy:** > 6h40min

!!! Note

    - LattePanda 3 Delta 3A is the current relative to its requirement in terms
      of USB-C Power Delivery (PD) compliant power banks (3A @ 15VDC)

### 2D Navigation (UST-10LX)

**Total Power Budget handled by the LiPo Battery**

| Source | Voltage (V) | Current (A) | Power (W) |
| :--- | :---: | :---: | :---: |
| 4 x Faulhaber 2342 OEM DC motors | 12V | 4 x 1.1A | 4 x 11W |
| 1 x Arduino Mega 2560 | 12V | 0.750A | - |
| 1 x Brainboxes SW-005 Ethernet Switch | 5-30V | - | 1.1W |
| 1 x Hokuyo UST-10LX | 10-30V | - | 3.6W @ 24VDC |

- **Power Consumption:** 57.7W _(estimated)_
- **Current Consumption:** 5.2A @ 11.1VDC
- **Autonomy:** > 1h55min

!!! Note

    - Faulhaber 2342 OEM DC motors 1.1A and 11W are the rated current and power,
      respectively (typically, given that robot carries a low load, should be
      much less than 1.1A continuously)
    - Arduino Mega 2560 current consumption was considered the maximum one
      supported by the SPX1117M3-L-5-0/TR DC Regulator for the PWRIN power input
      (750mA)
    - Brainboxes SW-005 Ethernet Switch 1.1W is the maximum power drawn
    - Hokuyo UST-10LX current consumption of 0.150A (equivalent to the 3.6W @
      24VDC) is the nominal supply current

**Total Power Budget handled by a 20000mAh 50W Power Bank for the Computing Unit**

| Source | Voltage (V) | Current (A) | Power (W) |
| :--- | :---: | :---: | :---: |
| 1 x LattePanda 3 Delta | 15V | 3A | - |

- **Power Consumption:** 45W _(estimated)_
- **Current Consumption:** 3A @ 15VDC
- **Autonomy:** > 6h40min

!!! Note

    - LattePanda 3 Delta 3A is the current relative to its requirement in terms
      of USB-C Power Delivery (PD) compliant power banks (3A @ 15VDC)

### 3D Navigation (RS-HELIOS-5515, UST-10LX)

**Total Power Budget handled by the LiPo Battery**

| Source | Voltage (V) | Current (A) | Power (W) |
| :--- | :---: | :---: | :---: |
| 4 x Faulhaber 2342 OEM DC motors | 12V | 4 x 1.1A | 4 x 11W |
| 1 x Arduino Mega 2560 | 12V | 0.750A | - |
| 1 x Brainboxes SW-005 Ethernet Switch | 5-30V | - | 1.1W |
| 1 x Hokuyo UST-10LX | 10-30V | - | 3.6W @ 24VDC |
| 1 x RoboSense RS-HELIOS-5515 | 9-32V | - | 12W |

- **Power Consumption:** 69.7W _(estimated)_
- **Current Consumption:** 6.3A @ 11.1VDC
- **Autonomy:** > 1h35min

!!! Note

    - Faulhaber 2342 OEM DC motors 1.1A and 11W are the rated current and power,
      respectively (typically, given that robot carries a low load, should be
      much less than 1.1A continuously)
    - Arduino Mega 2560 current consumption was considered the maximum one
      supported by the SPX1117M3-L-5-0/TR DC Regulator for the PWRIN power input
      (750mA)
    - Brainboxes SW-005 Ethernet Switch 1.1W is the maximum power drawn
    - Hokuyo UST-10LX current consumption of 0.150A (equivalent to the 3.6W @
      24VDC) is the nominal supply current
    - RoboSense RS-HELIOS-5515 12W is the typicall power drawn by the sensor

**Total Power Budget handled by a 20000mAh 50W Power Bank for the Computing Unit**

| Source | Voltage (V) | Current (A) | Power (W) |
| :--- | :---: | :---: | :---: |
| 1 x LattePanda 3 Delta | 15V | 3A | - |

- **Power Consumption:** 45W _(estimated)_
- **Current Consumption:** 3A @ 15VDC
- **Autonomy:** > 6h40min

!!! Note

    - LattePanda 3 Delta 3A is the current relative to its requirement in terms
      of USB-C Power Delivery (PD) compliant power banks (3A @ 15VDC)

### 2D Navigation and RGBD Perception (UST-10LX, L515)

**Total Power Budget handled by the LiPo Battery**

| Source | Voltage (V) | Current (A) | Power (W) |
| :--- | :---: | :---: | :---: |
| 4 x Faulhaber 2342 OEM DC motors | 12V | 4 x 1.1A | 4 x 11W |
| 1 x Arduino Mega 2560 | 12V | 0.750A | - |
| 1 x Brainboxes SW-005 Ethernet Switch | 5-30V | - | 1.1W |
| 1 x Hokuyo UST-10LX | 10-30V | - | 3.6W @ 24VDC |

- **Power Consumption:** 57.7W _(estimated)_
- **Current Consumption:** 5.2A @ 11.1VDC
- **Autonomy:** > 1h55min

!!! Note

    - Faulhaber 2342 OEM DC motors 1.1A and 11W are the rated current and power,
      respectively (typically, given that robot carries a low load, should be
      much less than 1.1A continuously)
    - Arduino Mega 2560 current consumption was considered the maximum one
      supported by the SPX1117M3-L-5-0/TR DC Regulator for the PWRIN power input
      (750mA)
    - Brainboxes SW-005 Ethernet Switch 1.1W is the maximum power drawn
    - Hokuyo UST-10LX current consumption of 0.150A (equivalent to the 3.6W at
      24VDC) is the nominal supply current

**Total Power Budget handled by a 20000mAh 50W Power Bank for the Computing Unit**

| Source | Voltage (V) | Current (A) | Power (W) |
| :--- | :---: | :---: | :---: |
| 1 x LattePanda 3 Delta | 15V | 3A | - |
| 1 x Intel RealSense L515 | 5V | - | 3.3W |

- **Power Consumption:** 48.3W _(estimated)_
- **Current Consumption:** 3.2A @ 15VDC
- **Autonomy:** > 6h15min

!!! Note

    - LattePanda 3 Delta 3A is the current relative to its requirement in terms
      of USB-C Power Delivery (PD) compliant power banks (3A @ 15VDC)
    - Intel RealSense L515 3.3W is the estimated power consumption of the sensor
      when in _Depth (XGA) + RGB (1080p, 30FPS)_ operation mode

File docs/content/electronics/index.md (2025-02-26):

# Electronics

The electronics of the original platform are completely revised in this work.
The original Discovery Q2 has some drawbacks that hinder its usage for robotics
Research & Development (R&D):

- no computing unit to allow the usage of the Robot Operating System (ROS)
  with the robot
- no wheeled odometry data available to the user
- no interface with the original motor drivers board to allow modifications on
  the internal closed-loop speed control of the wheels / linear and angular
  velocity control of the robot
- only a 5V @ 5A DC external output for the user (limiting the possibilities of
  powering multiple sensors such as 2D/3D LiDAR)
- does not support natively 3D LiDAR or RGBD cameras

As a result, this work completely over overhauls the original electronics, only
leaving the Faulhaber 2342 motors present in the original Hangfa Discovery Q2
platform.

## Overview

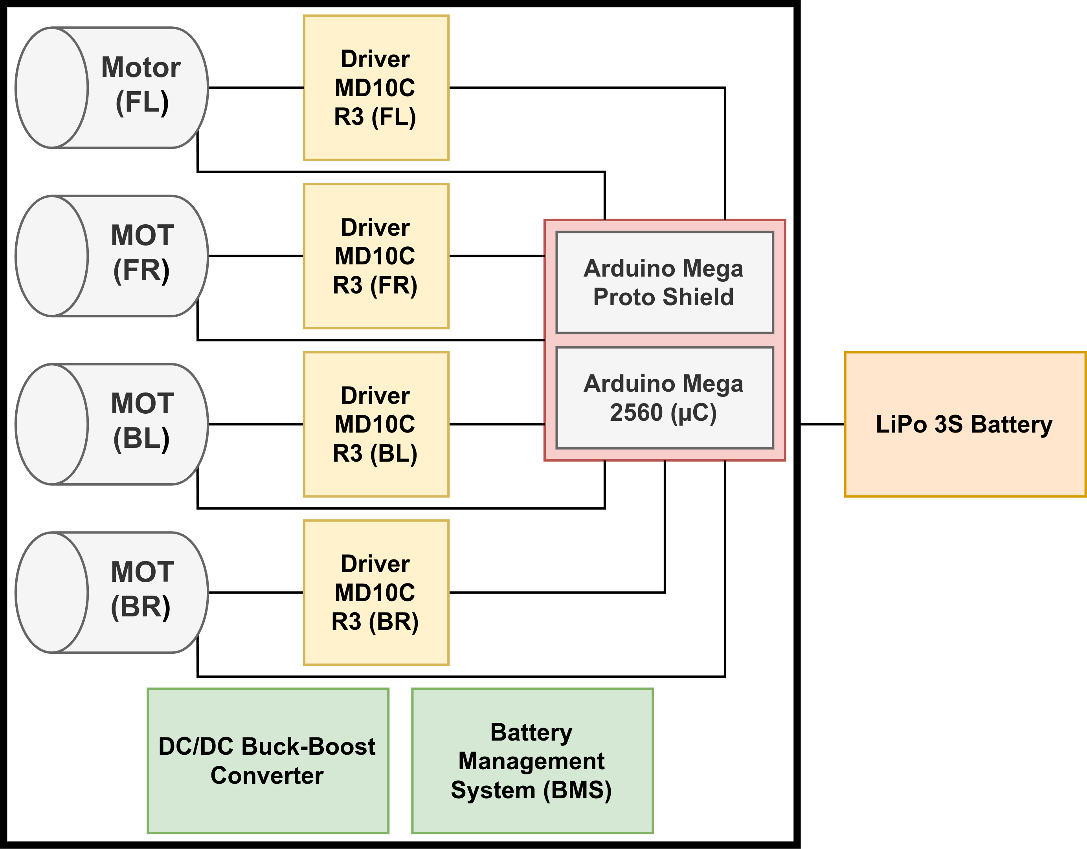
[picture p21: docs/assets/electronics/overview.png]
Electronics Overview


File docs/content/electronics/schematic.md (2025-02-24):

# Schematic

<div>
  <object data="../../../assets/electronics/schematic.pdf" type="application/pdf"
          width="100%" style="aspect-ratio:297/210;">
    <p>
      This browser does not support PDF! Click
      <a href="../../../assets/electronics/schematic.pdf">here</a>
      to download the file.
    </p>
  </object>
</div>

## Documents

- [schematic.pdf](../../assets/electronics/schematic.pdf)
- [schematic_easyeda.json](../../assets/electronics/schematic_easyeda.json)

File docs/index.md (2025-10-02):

# Integrating Multimodal Perception into Ground Mobile Robots

!!! Abstract

    Multimodal perception systems enhance the robustness and adaptability
    of autonomous mobile robots by integrating heterogeneous sensor modalities,
    improving long-term localisation and mapping in dynamic environments and
    human-robot interaction. Current mobile platforms often focus on specific
    sensor configurations and prioritise cost-effectiveness, possibly limiting
    the flexibility of the user to extend the original robots further.
    This paper presents a methodology to integrate multimodal perception into a
    ground mobile platform, incorporating wheel odometry, 2D laser scanners,
    3D Light Detection and Ranging (LiDAR), and RGBD cameras.
    The methodology describes the electronics design to power devices, firmware,
    computation and networking architecture aspects, and mechanical mounting
    for the sensory system based on 3D printing, laser cutting, and
    bending metal sheet processes. Experiments demonstrate the usage of the
    revised platform in 2D and 3D localisation and mapping and pallet pocket
    estimation applications. All the documentation and designs are accessible
    in a public repository.

    **Keywords:**
    Light Detection and Ranging (LiDAR),
    mobile robot,
    multimodal perception,
    open-source,
    RGBD camera.

This repository contains all the documentation associated with the modifications
made by [INESC TEC](https://www.inesctec.pt/en/) on the
[Hangfa Discovery Q2](https://www.hangfa-europe.com/en/omni-robot/discovery)
mobile platform in order to be compatible with multimodal perception. These
modifications also enable the platform to be integrated in the
[Robot Operating System (ROS)](https://ros.org/), facilitating its usage for
research topics such as perception, localisation and mapping, multi-robot
coordination (when more than one platform is available to the user), Artificial
Intelligence (AI) applied on autonomous mobile robotics, among other topics.

Furthermore, the main goals of this website and the respective GitHub repository
is to help researchers interested in modifying their Hangfa mobile platforms or
applying all the modifications that we have made to other similarly small mobile
platforms. As a result, the website includes the following information:

- **[Platform](content/discovery-q2.md):** brief presentation of the
  [Hangfa Discovery Q2](https://www.hangfa-europe.com/en/omni-robot/discovery)
  robot mobile platform
- **[Bill Of Materials (BOM)](content/bom.md):** summary on the components used for
  the modifications to the platform
- **[Electronics](content/electronics/index.md):** presentation of the electronics redesign
  (battery management and power budgets, motor drivers, encoders reading, and
  external DC power output for the user)
- **[Single Board Computer (SBC)](content/sbc/index.md):** computing units
  considered in the work and their configuration in terms of Operating System
  (OS), Robot Operating System (ROS) setup, configuring remote access, set up
  development environment, and configuring the firmware communication
- **[Network](content/):** TBC
- **[Sensors](content/):** TBC
- ... _To Be Completed (TBC)_

Lastly, this work is within the scope of the
[Mobile Robotics Development Team (MRDT)](https://gitlab.inesctec.pt/mrdt/) in
the national project
[GreenAuto: Green innovation for the Automotive Industry](https://transparencia.gov.pt/en/fundos-europeus/prr/beneficiarios-projetos/projeto/02/C05-i01.02/2022.PC644867037-00000013/). [MRDT](https://gitlab.inesctec.pt/mrdt/) team is a
Research & Development (R&D) team from the
[CRIIS - Centre for Robotics in Industry and Intelligent Systems](https://www.inesctec.pt/en/centres/criis)
at the [iiLab - Industry and Innovation Laboratory](https://www.inesctec.pt/en/laboratories/iilab-industry-and-innovation-lab).

## Videos

<iframe width="560" height="315" src="https://www.youtube.com/embed/videoseries?si=M_ykKm2IiWBJxEFs&amp;list=PLvp8fJUEPxYSkKsOrCN5FzjuhhSfVgSuR" title="YouTube video player" frameborder="0" allow="accelerometer; autoplay; clipboard-write; encrypted-media; gyroscope; picture-in-picture; web-share" referrerpolicy="strict-origin-when-cross-origin" allowfullscreen></iframe>

- **How To Watch**
    1. Press the :material-play: Play button
    2. Use the :material-skip-previous: Previous and :material-skip-next: Next
       buttons to navigate through the playlist
- **Playlist YouTube Link:**
  [https://youtube.com/playlist?list=PLvp8fJUEPxYSkKsOrCN5FzjuhhSfVgSuR&si=SDjPObDUzQucRvuN](https://youtube.com/playlist?list=PLvp8fJUEPxYSkKsOrCN5FzjuhhSfVgSuR&si=SDjPObDUzQucRvuN)

## History

The Hangfa Discovery Q2 platforms were firstly used at
[CRIIS - Centre for Robotics in Industry and Intelligent Systems](https://www.inesctec.pt/en/centres/criis)
from
[INESC TEC - Institute for Systems and Computer Engineering, Technology and Science](https://www.inesctec.pt/en)
by a student in 2016. This student was Fernando Jorge Marques de Sá, being
enrolled in the Master of Science (MSc) course in Electrical and Computers
Engineering (ECE) at the
[Faculty of Engineering, University of Porto (FEUP)](https://sigarra.up.pt/feup/en/).
The modifications made to the Hangfa platform in order to make it compatible
with perception and Simultaneous and Localization and Mapping (SLAM) on mobile
ground robots were not developed during Fernando's MSc Thesis.
Nevertheless, those modifications were possible given the knowledge gained in
terms of the platform limitations and usage.

**Citation**

> Fernando Jorge Marques de Sá (2016).
> _Sistema de navegação para plataforma móvel omnidirecional_
> [Master's thesis, Faculty of Engineering, University of Porto (FEUP)].
> Open Repository of the University of Porto.
> URI: https://hdl.handle.net/10216/85263

**Document**

- [msc-thesis.pdf](assets/msc-thesis/msc-thesis_fernando-sa_navigation-system-for-omnidirectional-mobile-platform.pdf)

## Contacts

If you have any questions or you want to know more about this work, please
contact one of the following contributors:

- Ricardo B. Sousa
  ([rbs@fe.up.pt](mailto:rbs@fe.up.pt))
  _(Corresponding Author)_
  [:fontawesome-brands-github:](https://github.com/sousarbarb/),
  [:fontawesome-brands-gitlab:](https://gitlab.com/sousarbarb/),
  [:fontawesome-brands-gitlab:](https://gitlab.inesctec.pt/ricardo.b.sousa),
  [:fontawesome-brands-orcid:](https://orcid.org/0000-0003-4537-5095),
  [:fontawesome-brands-google-scholar:](https://scholar.google.pt/citations?user=Bz2FMqYAAAAJ),
  [:fontawesome-brands-linkedin:](https://www.linkedin.com/in/sousa-ricardob/),
  [:fontawesome-brands-youtube:](https://www.youtube.com/channel/UCXTR8mMlG0VOC_06PKg5KBQ)
- Héber Miguel Sobreira
  ([heber.m.sobreira@inesctec.pt](mailto:heber.m.sobreira@inesctec.pt))
  [:fontawesome-brands-github:](https://github.com/HeberSobreira),
  [:fontawesome-brands-gitlab:](https://gitlab.inesctec.pt/heber.m.sobreira/),
  [:fontawesome-brands-orcid:](https://orcid.org/0000-0002-8055-1093),
  [:fontawesome-brands-google-scholar:](https://scholar.google.pt/citations?user=iNhGcpsAAAAJ)
- João G. Martins
  ([joao.g.martins@inesctec.pt](mailto:joao.g.martins@inesctec.pt))
  [:fontawesome-brands-github:](https://github.com/Joao-G-Martins),
  [:fontawesome-brands-orcid:](https://orcid.org/0000-0002-6567-4802)
- Paulo G. Costa
  ([paco@fe.up.pt](mailto:paco@fe.up.pt))
  [:fontawesome-brands-github:](https://github.com/P33a),
  [:fontawesome-brands-orcid:](https://orcid.org/0000-0002-4846-271X),
  [:fontawesome-brands-google-scholar:](https://scholar.google.pt/citations?user=7Iz8fKcAAAAJ)
- Manuel F. Silva
  ([mss@isep.ipp.pt](mailto:mss@isep.ipp.pt))
  [:fontawesome-brands-orcid:](https://orcid.org/0000-0002-0593-2865),
  [:fontawesome-brands-google-scholar:](https://scholar.google.pt/citations?user=2EFVZ-AAAAAJ)
- António Paulo Moreira
  ([amoreira@fe.up.pt](mailto:amoreira@fe.up.pt))
  [:fontawesome-brands-orcid:](https://orcid.org/0000-0001-8573-3147),
  [:fontawesome-brands-google-scholar:](https://scholar.google.pt/citations?user=eL0gHLoAAAAJ)

## Institutions

<div class="grid cards" markdown>

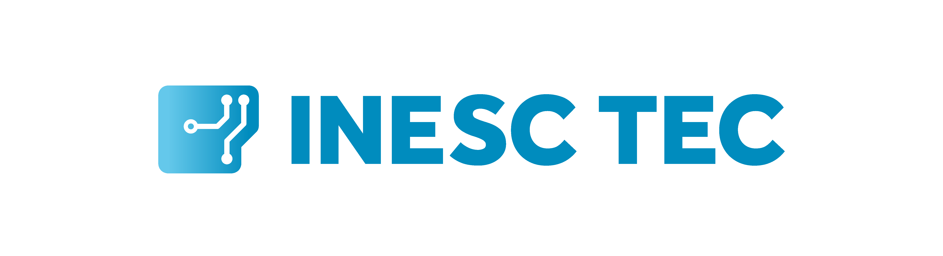
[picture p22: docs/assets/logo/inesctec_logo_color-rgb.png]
INESC TEC Logo (https://www.inesctec.pt/en/)
- 
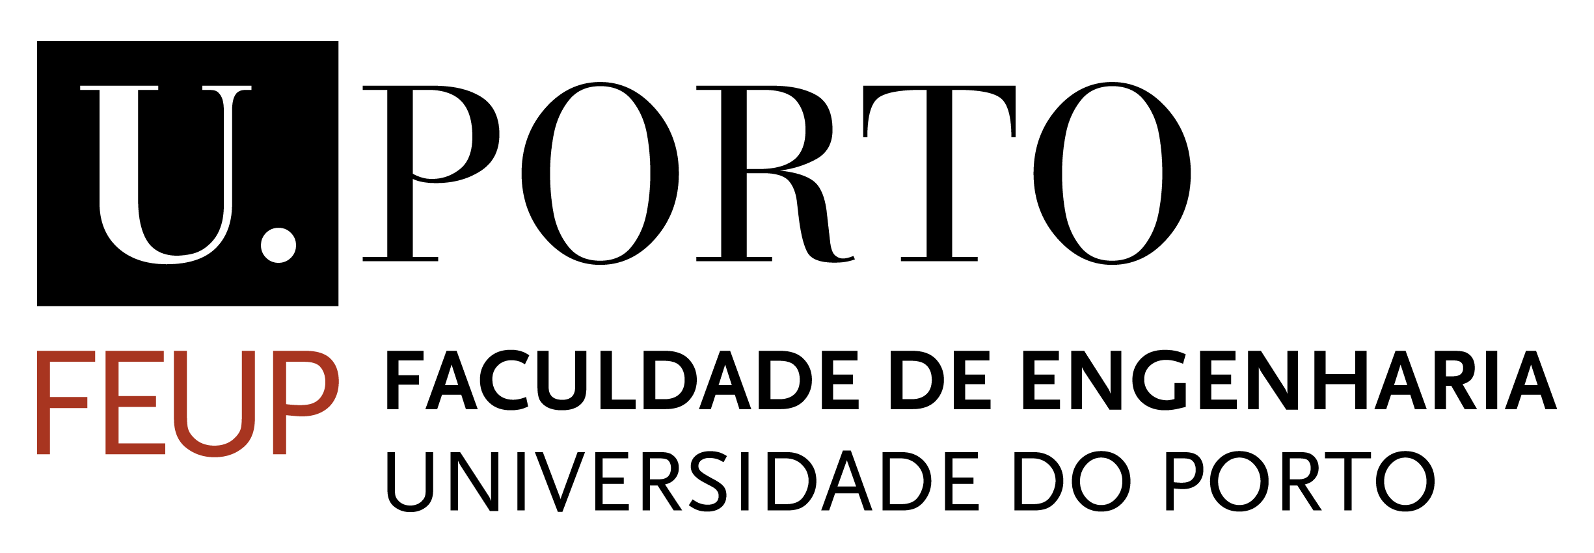
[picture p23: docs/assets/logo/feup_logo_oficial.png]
FEUP Logo (https://sigarra.up.pt/feup/en/)
- 

</div>

## Acknowledgements

<div class="grid cards" markdown>

- **[5dpo Robotics Team](https://5dpo.github.io/)**
- Amorins & Silva Logo (https://amorinsesilva.pt/)
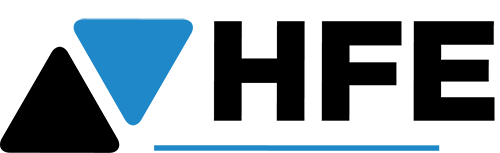
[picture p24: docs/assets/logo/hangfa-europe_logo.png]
Hangfa Robotics Europe Logo (https://www.hangfa-europe.com/)
- 
- LattePanda Logo (https://www.lattepanda.com/)

</div>

## Funding

**GreenAuto: Green innovation for the Automotive Industry**

This work is co-financed by Component 5 - Capitalization and Business
Innovation, integrated in the Resilience Dimension of the Recovery and
Resilience Plan within the scope of the Recovery and Resilience Mechanism (MRR)
of the European Union (EU), framed in the Next Generation EU, for the period
2021 - 2026, within project GreenAuto, with reference 54.

- **Operation Code:** 02/C05-i01.02/2022.PC644867037-00000013
- **Beneficiary:** Peugeot Citröen Automóveis Portugal, S.A.
- **Work Package:** WP10 - Automated logistics for the automotive industry
- **Product, Processes, or Services (PPS):**
  PPS18 - 3D navigation system for mobile robotic equipment
- **Consortium Partners:**
    - [Flowbotic Mobile Systems, Lda](https://www.flowbotic.eu/) _(leader)_
    - [Faculty of Engineering, University of Porto (FEUP)](https://www.up.pt/feup/en/)
    - [INESC TEC - Institute for Systems and Computer Engineering, Technology and Science](https://www.inesctec.pt/en/)
    - [STAR](https://starinstitute.pt/)
    - [Kaizen](https://kaizen.com/pt-pt/)
    - [Institute for Systems and Robotics (ISR)-Coimbra](https://www.isr.uc.pt/)
- **Timeline:** October 2021 - December 2025
- **Duration:** 51 months
- **URL:**
  [https://transparencia.gov.pt/en/fundos-europeus/prr/beneficiarios-projetos/projeto/02/C05-i01.02/2022.PC644867037-00000013/](https://transparencia.gov.pt/en/fundos-europeus/prr/beneficiarios-projetos/projeto/02/C05-i01.02/2022.PC644867037-00000013/)

## Citation

**Plain Text**

R.B. Sousa, H.M. Sobreira, J.G. Martins, P.G. Costa, M.F. Silva and A.P.
Moreira,
"Integrating Multimodal Perception into Ground Mobile Robots,"
_2025 IEEE International Conference on Autonomous Robot Systems and_
_Competitions (ICARSC2025)_, Madeira, Portugal, 2025, pp. 104-111,
doi: [10.1109/ICARSC65809.2025.10970176](https://doi.org/10.1109/ICARSC65809.2025.10970176).
[[github]](https://github.com/sousarbarb/inesctec_mrdt_hangfa_discovery_q2)
[[preprint]](http://doi.org/10.13140/RG.2.2.29381.15845/1)

**BibTex**

```bibtex
@INPROCEEDINGS{sousa2025icarsc,
  author    = {Ricardo B. Sousa and Héber Miguel Sobreira and João G. Martins and Paulo G. Costa and Manuel F. Silva and António P. Moreira},
  booktitle = {2025 IEEE International Conference on Autonomous Robot Systems and Competitions (ICARSC)},
  title     = {Integrating Multimodal Perception into Ground Mobile Robots},
  year      = {2025},
  volume    = {},
  number    = {},
  pages     = {104--111},
  doi       = {10.1109/ICARSC65809.2025.10970176},}
```

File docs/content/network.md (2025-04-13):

# Network Configuration

The [LattePanda 3 Delta](https://www.lattepanda.com/lattepanda-3-delta) SBC has
only a single Ethernet port. In order to allow multiple sensors that use
Ethernet communicating simultaneously with the SBC, we use an Ethernet switch to
create a Local Access Network (LAN) between the SBC and the sensors (e.g., 2D
laser scanners or 3D LiDARs). Then, the SBC acts as the access point to
local available networks in the deployment site of the mobile platform.
The connection to external networks is through Wi-Fi using the
Bingfu Antena WiFi Dual Band RP-SMA 25cm U.FL IPX IPEX MHF4 M.2 NGFF Intel
to boost the [LattePanda 3 Delta](https://www.lattepanda.com/lattepanda-3-delta)
SBC wireless connectivity.

## Overview

Networking Architecture Overview

## Ethernet Switch

Given that the network architecture employed in this work does not have a router
on-board the robot, we opted for unmanaged switches due to being plug-and-play
and do not require any configuration. As a result, the Ethernet switch models
considered are from Brainboxes, depending on the desired data transmission speed:

- Brainboxes SW-005
  ([url](https://www.brainboxes.com/product/industrial-ethernet-switches/fast-ethernet/sw-005),
  [datasheet](../assets/networking/ethernet-switch_brainboxes-sw-005_datasheet.pdf))
    - 5 port 10/100Mbps
    - Unregulated +5-30VDC input power
- Brainboxes SW-015
  ([url](https://www.brainboxes.com/product/industrial-ethernet-switches/gigabit-ethernet/sw-015),
  [datasheet](../assets/networking/ethernet-switch_brainboxes-gigabit-switch-range_datasheet.pdf))
    - 5 port 1Gbps
    - Unregulated +5-30VDC input power

## Gallery

LattePanda 3 Delta, Xiaomi Power Bank, and Ethernet Switch

- **A:** Brainboxes SW-005 Ethernet Switch
- **B:** Powerbank Xiaomi Mi 50W 20000 mAh
- **C:** LattePanda 3 Delta SBC
- **D:** Bingfu Antena WiFi Dual Band RP-SMA 25cm U.FL IPX IPEX MHF4
  M.2 NGFF Intel

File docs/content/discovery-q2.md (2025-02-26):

# Hangfa Discovery Q2

The Discovery Q2 is a small robot platform developed by
[HANGFA Robotics](https://www.hangfa-europe.com/).
This platform is a four-wheeled omnidirectional robot with 4 QMA10 mecanum
wheels driven by 4 coreless servo motors, supporting CAN bus and RS232 serial
ports. The original plaform provides a Software Development Kit (SDK), allowing
users to extend the capabilities of the plaform. This SDK provides a complete
communication protocol and source code samples based on the STM32F407.

## Links

- [HANGFA Robotics Europe](https://www.hangfa-europe.com/)
- [Discovery Series](http://www.cdhfyy.com/EN/robot/Discovery.html)
  _(Chengdu HANGFA Hydraulic Engineering Co. Ltd)_
- [Discovery Series](https://www.hangfa-europe.com/en/omni-robot/discovery)
  _(HANGFA Robotics Europe)_
- [Discovery Q2](http://www.cdhfyy.com/EN/robot/DiscoveryQ2.html)
- [QMA Mecanum Wheel Series](http://www.cdhfyy.com/EN/omniwheel/QMA.html)
  _(Chengdu HANGFA Hydraulic Engineering Co. Ltd)_
- [QMA Mecanum Wheel Series](https://www.hangfa-europe.com/en/mecanum-wheels/qma-series)
  _(HANGFA Robotics Europe)_
- [QMA10 Mecanum Wheel](http://www.cdhfyy.com/EN/omniwheel/QMA10.html)

## Documents

- [Hangfa Discovery Q2 User Manual](../assets/platform/hangfa-discovery-q2_user-manual.pdf)
- [Hangfa Discovery Q2 Robot Main Control Board (RHF407) User Manual](../assets/platform/hangfa-discovery-q2_rhf407-user-manual.pdf)
- [Hangfa Discovery Q2 Dimensions](../assets/platform/hangfa-discovery-q2_dimensions.pdf)
  (available at
  [http://www.hangfa.com/products/research-platform/discoveryQ2.html](http://www.hangfa.com/products/research-platform/discoveryQ2.html))
- [Hangfa Compass Q2 User Manual](../assets/platform/hangfa-compass-q2_user-manual.pdf)
  (available at
  [https://cdn.robotshop.com/media/h/hfa/rb-hfa-01/pdf/compass_q2_user_manual_1.2.pdf](https://cdn.robotshop.com/media/h/hfa/rb-hfa-01/pdf/compass_q2_user_manual_1.2.pdf))

## Characteristics

| Description | Value |
| :--- | :---: |
| Body Structure | aluminum alloy (bent yellow metal sheets) |
| Dimensions | 359x313.5x114mm |
| Weight | 7kg |
| Ground Clearance | 23mm |
| Type | four-wheeled omnidirectional |
| Maximum Translational Speed | 0.65m/s |
| Maximum Rotational Speed | 140º/s |
| Autonomy | >10h @ 3kg load, 0.5m/s, 70% moving rate |
| Wheels | QMA10 mecanum (Hangfa) |
| Wheels Structure | carbon steel hub |
| Wheels Dimensions | 101.6mm (diameter) x 45.7mm (wide) |
| Wheels Weight | 350g |
| Wheels Maximum Load | 30kg |
| Wheels #Rollers | 10 |
| Wheels Rollers Structure | two bearings fixation, rubber surface |
| Motors Model | Faulhaber 2342 OEM DC motor |
| Motors Voltage (Rated) | 12V |
| Motors Current (Rated) | 1.1A |
| Motors Output Power (Rated) | 11W |
| Motors Speed (Rated) | 5800rpm |
| Motors Speed (No-load) | 6800rpm |
| Motors Encoders | 5V, 2 channels, 12CPR |
| Motors Fixation Type | outer body bearing block bears the wheel in axial and radial loads |
| Motor Drivers | IMDR4 module boards |
| Motor Drivers Interfaces | CAN, RS232 |
| Battery | 12V DC 10400mAh Li-ion |
| Battery Charger | KXD-126300 Li-ion charger, 100~240VAC input, 12.6VDC @ 3.0A output |
| External User Power | 5V @ 5A DC |
| Electrical Protection | 10A power fuse |

## Gallery

<div class="grid" markdown>











</div>

## Limitations for Multimodal Perception

- No computer unit included to, e.g., run Robot Operating System (ROS)-based
  executable nodes
- Wheeled odometry data not available
- IMDR4 board does not have an interface to change the internal closed-loop
  control if needed
- Only 5V @ 5A external output provided to the user
- No native support for 3D LiDAR and RGBD cameras

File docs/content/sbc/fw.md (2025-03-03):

# Firmware Setup

## Device Rules (udev)

### PlatformIO Devices

```sh
curl -fsSL https://raw.githubusercontent.com/platformio/platformio-core/develop/platformio/assets/system/99-platformio-udev.rules | sudo tee /etc/udev/rules.d/99-platformio-udev.rules
sudo service udev restart
```

Source:
[https://docs.platformio.org/en/latest/core/installation/udev-rules.html#platformio-udev-rules](https://docs.platformio.org/en/latest/core/installation/udev-rules.html#platformio-udev-rules).

### Specific Device Rules

!!! Tip

    Specific device rules allows to define a particular name for a certain
    device, allowing static naming when connection through serial port
    communication.

    In particularly with LattePanda SBCs, this feature is even more important
    to separate clearly which device is one (depending on the restart of the
    SBC with an Arduino or other device already plugged into the LattePanda,
    the onboard ATMega32 may be either `/dev/ttyACM0` or `/dev/ttyACM1`).

    Source:
    [https://roboticsknowledgebase.com/wiki/tools/udev-rules/](https://roboticsknowledgebase.com/wiki/tools/udev-rules/).

1. Open :material-microsoft-visual-studio-code: Visual Studio Code
    - GNOME menu
    - Terminal (`$ code` | `$ code .` to open the VS Code in the current
      directory)
2. Open :simple-platformio: PlatformIO extension
    - PIO Home :material-arrow-right: Devices
        - `/dev/ttyACM0`
            - Description: `LattePanda Leonardo`
            - Hardware: `USB VID:PID=3343:803A LOCATION=1-5:1.0`
        - `/dev/ttyACM1`
            - Description: `ttyACM1`
            - Hardware: `USB VID:PID=2341:0042 SER=9593132393135171D1E2 LOCATION=1-2:1.0`

    !!! Tip

        Another way to check the previous information is directly through
        terminal commands:

        ```sh
        udevadm info -a -n /dev/ttyACM0
        udevadm info -a -n /dev/ttyACM1
        ```

3. Execute the following commands

    ```sh
    sudo touch /etc/udev/rules.d/99-usb-serial.rules
    sudo tee /etc/udev/rules.d/99-usb-serial.rules <<EOF
    # LattePanda Leonardo (ATMega32 onboard of the SBC)
    SUBSYSTEM=="tty", ATTRS{idVendor}=="3343", ATTRS{idProduct}=="803a", SYMLINK+="ttyLattePandaATMega"

    # Arduino Mega
    SUBSYSTEM=="tty", ATTRS{idVendor}=="2341", ATTRS{idProduct}=="0042", SYMLINK+="ttyArduinoMega"

    EOF
    ```

## CoolTerm

!!! Tip

    CoolTerm is a more advanced serial monitor with an User Interface (UI),
    compared to the native serial monitor implementation of PlatformIO.

1. Download CoolTerm (available at
   [https://freeware.the-meiers.org/](https://freeware.the-meiers.org/))
2. Execute the following commands
    ```sh
    mkdir ~/dev/tools -p
    mv ~/Downloads/CoolTermLinux64Bit.zip ~/dev/tools/

    cd ~/dev/tools/
    unzip CoolTermLinux64Bit.zip
    ```
3. Open CoolTerm
    ```sh
    cd ~/
    ./dev/tools/CoolTermLinux64Bit/CoolTerm
    ```
4. Connection :material-arrow-right: Options
    - Serial Port
        - Port: `/dev/ttyACM1` _(note that LattePanda SBCs comes with ATMega32)_
        - Baudrate: `115200` _(check in your code the serial port's baud rate)_
        - Data bits: `8`
        - Parity: `None`
        - Stop bits: `1`
    - Receive
        - Enable _Direct RX update of text display_
        - Enable _Add timestamps to received data_

            !!! Tip

                Enabling timestamps may be useful to check the cycle time
                period.

        - Set _Type_ to _Time + Milliseconds_

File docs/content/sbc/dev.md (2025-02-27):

# Development Environment

## Doxygen

```sh
sudo apt update
sudo apt install doxygen doxygen-doc doxygen-latex -y
```

## Visual Studio Code

### Installation

1. Download :material-microsoft-visual-studio-code: Visual Studio Code
   (available at
   [https://code.visualstudio.com/download](https://code.visualstudio.com/download))
2. Execute the following commands
    ```sh
    cd ~/Downloads/
    sudo apt install ./code_1.97.2-1739406807_amd64.deb -y
    ```

### Setup

1. Open :material-microsoft-visual-studio-code: Visual Studio Code
    - GNOME menu
    - Terminal (`$ code` | `$ code .` to open the VS Code in the current
      directory)
2. :material-view-grid-plus-outline: Extensions
   (**++ctrl+shift+x++** | File :material-arrow-right: Preferences
   :material-arrow-right: Extensions)
    - :simple-cplusplus: ms-vscode.cpptools-extension-pack
        - ms-vscode.cpptools
        - ms-vscode.cpptools-themes
        - ms-vscode.cmake-tools
    - :material-language-python: ms-python.python
    - :material-language-python: ms-python.debugpy
    - :material-language-python: ms-python.vscode-pylance
    - :simple-doxygen: cschlosser.doxdocgen
    - :simple-ros: :material-robot: ms-iot.vscode-ros
    - :material-file-xml-box: :material-xml: redhat.vscode-xml
    - :simple-yaml: redhat.vscode-yaml
    - :material-file-pdf-box: tomoki1207.pdf
    - :simple-platformio: platformio.platformio-ide

        !!! Warning

            PlatformIO requires the Python Virtual Environment to be installed
            as well as possibly needing to have `python` as an alias to
            `python3`
            ([https://docs.platformio.org/en/latest/faq/install-python.html](https://docs.platformio.org/en/latest/faq/install-python.html)).

            ```sh
            sudo apt install python-is-python3 python3-venv -y
            ```

    - :material-owl: sdras.night-owl

3. User settings (**++ctrl+shift+p++** :material-arrow-right:
   _Preferences: Open User Settings (JSON)_)
    ```json title="settings.json"
    {
        "editor.renderWhitespace": "none",
        "editor.tabSize": 2,
        "files.trimTrailingWhitespace": true,
        "files.trimFinalNewlines": true,
        "editor.rulers": [
            80, 120
        ],
        "cmake.configureOnOpen": false,
        "workbench.colorTheme": "Night Owl",
        "explorer.confirmDragAndDrop": false,
        "explorer.confirmDelete": false,
        "terminal.integrated.stickyScroll.enabled": false,
        "git.openRepositoryInParentFolders": "always",
        "window.title": "${dirty}${rootName}"
    }
    ```

## SSH Network Shared Folder

1. Open :material-folder: File Explorer (**++super+e++**)
2. :material-plus: Other Locations :material-arrow-right: Connect to Server
    - Connect to Server: `ssh://user@discoveryq2/home/user/`

## SSH Keys

1. Execute the following commands
    ```sh
    ssh-keygen -t ed25519 -C "discoveryq2@inesctec.pt"
    eval $(ssh-agent -s)
    ssh-add .ssh/id_ed25519
    ```
2. Copy the contents of your public key file
    ```sh
    xclip -sel c < ~/.ssh/id_ed25519.pub  # (1)!
    cat ~/.ssh/id_ed25519.pub
    ```

    1. This command may not work when access your robot through a non graphical
       interface.

3. Sign in to GitLab
4. On the left sidebar, select your avatar
5. Select _Edit profile_
6. On the left sidebar, select _SSH Keys_
7. Select _Add new key_
8. Verify that you can connect

    ```sh
    ssh -T git@gitlab.inesctec.pt
    ```

More information in
[https://docs.gitlab.com/user/ssh/](https://docs.gitlab.com/user/ssh/).

!!! Tip

    In order to avoid setting up the `~/.ssh/config` file, you can use the same
    SSH key for different Git servers.

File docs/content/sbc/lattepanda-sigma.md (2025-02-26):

# LattePanda Sigma

## Links

- [LattePanda Sigma](https://www.lattepanda.com/lattepanda-sigma)
- [LattePanda Specification](https://docs.lattepanda.com/content/sigma_edition/Specification/)
- [Pinout and Hardware Diagram](https://docs.lattepanda.com/content/sigma_edition/IO_Playability/)
- [Initial Setup of the Sigma by LattePanda](https://docs.lattepanda.com/content/sigma_edition/Getting_Started/)
- [LattePanda Sigma 3D Model](https://github.com/LattePandaTeam/LattePanda-3D-Models/tree/master/LattePanda%20Sigma)

## Specifications

| Component | Content | Specs. |
| :--- | --- | :--- |
| Processor | CPU | Intel® Core™ i5-1340P |
| | Cores / Threads | 12C(4P+8E) / 16T |
| | Max Turbo Frequency | 4.60 GHz(Performance-core), 3.4 GHz(Efficient-core) |
| | L2 Cache | 12 MB |
| | Base Power | 28 W  <br>(BIOS Default: PL1 45W, PL2 64W) |
| | Graphics | Intel® Iris® Xe Graphics |
| | Max Dynamic Frequency | 1.45 GHz |
| | Execution Units | 80 |
| | Co-processor | Microchip® ATmega32U4-MU |
| Memory | Technology | Dual-Channel, Samsung LPDDR5-6400(16GB), LPDDR5-6000(32GB) |
| | Capacity | 16GB，32GB |
| Storage | Drive Form Factor | M.2 SSD (NVMe/SATA), SATA Drive |
| Wireless | Wireless Form Factor | M.2 Wireless Module (PCIe/CNVio) |
| Display | HDMI Port | HDMI 2.1, Up to 4096 x 2304 @ 60Hz |
| | USB Type-C Port | DP 1.4a, Up to 7680 x 4320 @ 60Hz (One Monitor) |
| | eDP(Embedded Display Port) | eDP 1.4b, 4 Lanes, Up to 4096 x 2304 @ 120Hz |
| External I/O | USB Type-A | 2 x USB2.0 (480Mbps), 2 x USB3.2 Gen 2 (10Gbps) |
| | USB Type-C | 2 x Thunderbolt™ 4 (40Gbps) |
| | HDMI | HDMI 2.1 |
| | Ethernet | 2 x 2.5GbE RJ45 Ports (Intel® i225-V Gigabit Ethernet Controller, Supports 10/100/1000/2500 Mbps, WOL) |
| | Power | 5.5mm x 2.5mm DC Jack |
| | Audio | 3.5mm Microphone Headphone Combo Connector |
| | Sim Card | Micro Sim Card Slot |
| Internal I/O | USB 2.0 | 2.0mm Pitch 4-Pin Connector, 480Mbps |
| | Fan | 1.27mm Pitch,12V 4-Wire Fan Connector, PWM Control |
| | SATA | SATA 6.0 Gb/s Data Connector, 2.0mm Pitch 4-Pin Power Connector |
| | Front Panel | 2.54mm Pitch 9-Pin Header, Supports Power, Reset, Power LED, HDD LED |
| | Front Audio Panel | 2.54mm Pitch 9-Pin Header, Supports High Definition Audio (HD), Line-Out, Mic-in |
| | COM | 2.54mm Pitch 9-Pin Header,Supports RS232, RS485 |
| | GPIO | 2.54mm Pitch 34-Pin Header, Including ATmega32U4 I/O Pins, 5V Power Pins, S0/S3/S4 State Pins |
| | eDP | 0.5mm Pitch 40-Pin Connector, 4 Lanes |
| Expansion Slot | M.2 M Key | Type 2280, Supports PCIe 3.0 x4<br>Type 2280, Supports PCIe 4.0 x4 |
| | M.2 B Key | Type 2242/2252/2280, Supports SATA III/PCIe 3.0 x1, USB2.0, USB3.0, SIM |
| | M.2 E Key | Type 2230, Supports PCIe 3.0 x1,USB2.0, Intel CNVio |
| Security | TPM | Processor's Built-in TPM (2.0) |
| Power | Power Input | 5.5mm x 2.1mm DC Jack: DC 12~20V <br>USB Type C: PD 20V |
| | Attached Power Adapter | 19V DC, 4.74A, 90W |
| | RTC Battery | CR1220 Battery Holder: 3V <br>1.27mm Pitch 2-Pin Connector: 3V |
| Operating System | Microsoft Windows | Windows 10, Windows 11 |
| | Linux | Ubuntu, Promox VE, etc. |
| Environment | Operating Temperature | 0~45℃ |
| | Relative Humidity | 0%~80%RH |
| Dimension | Form Factor | 3.5", 146 x 102 mm |
| Model(SKU) | DFR1080 | LattePanda Sigma (16GB RAM, no SSD, no WiFi) |
| | DFR1081 | LattePanda Sigma (16GB RAM, 500GB PCIe 4.0 x4 NVMe SSD, Intel AX211 WiFi6E) |
| | DFR1090 | LattePanda Sigma (32GB RAM, no SSD, no WiFi) |
| | DFR1091 | LattePanda Sigma (32GB RAM, 500GB PCIe 4.0 x4 NVMe SSD, Intel AX211 WiFi6E) |
| Compliance | Certification | CE, FCC, KC, RoHS |

## Initial Setup

- :fontawesome-regular-hard-drive: M.2 NVMe SSD
- :material-cable-data:            HDMI Cable
- :material-monitor:               External HDMI Monitor
- :material-keyboard:              Keyboard and a Mouse
- :material-power-plug-battery:    Power Adapter
- :material-antenna:               M.2 Wireless Network Model with WIFI/BT antennas
    - M.2 (A+E Key) AX210 WiFi 6E Network Card for LattePanda Sigma, Alpha, Delta

**Instructions**

1. Connect an M.2 NVMe SSD to the M.2 Key-M socket
2. Install a compatible M.2 wireless network card
    - Intel AX210
    - Intel AX211 _(included in the LattePanda Sigma 32GB bundle DFR1091)_
    - Intel AX200
    - Intel AX201
    - Intel AC9560
    - Intel AC8265
3. _(optional)_ Install the LattePanda Sigma into a case
    - Aluminum Case for LattePanda Sigma Single Board Computer
    - Vertical M.2 Expansion Support Case in Aluminum Alloy
4. Connect an HDMI display
5. Connect the keyboard and mouse to the LattePanda 3 Delta
6. Connect the power adapter provided in the SBC's box
7. Press the power button and the blue LED indicator will light up
    - Default OS is Windows 10 :fontawesome-brands-windows:

!!! Warning

    This SBC appears to not have a working wireless connection in
    [Ubuntu 20.04.6 LTS](https://releases.ubuntu.com/focal/) due to missing
    drivers for the Intel AX211 M.2 wireless network card.

    An alternative is using a TP-Link WiFi USB, where you only have to install
    the following drivers:
    ```sh
    sudo apt update
    sudo apt dist-upgrade
    sudo apt install linux-headers-$(uname -r) build-essential git

    mkdir ~/dev/tools/ -p

    cd ~/dev/tools/
    git clone https://github.com/lwfinger/rtw88

    cd rtw88
    make
    sudo make install
    sudo make install_fw
    ```

## BIOS Setup

### Entering BIOS

**Default**

1. Power on or reboot LattePanda
2. Press **++del++** or **++esc++** key continuously to
   enter into BIOS menu before you see the LattePanda logo on the splash screen

**Windows 10**

1. Start Menu :fontawesome-brands-windows: :material-arrow-right:
   Press **++shift++** + Restart
2. Choose :material-tools: Troubleshoot :material-arrow-right: Advanced Options
   :material-arrow-right: UEFI Firmware Settings :material-arrow-right:
   Restart

### Auto Power-on

1. Power on the LattePanda and enter the BIOS
2. BIOS Setup :material-arrow-right: Advanced :material-arrow-right:
   Power Management :material-arrow-right: ACPowerLoss :material-arrow-right:
   Set the ACPowerLoss option to `PowerOn`
3. Save & Exit (Press **++f4++**)

### Configurable TDP

1. Power on the LattePanda and enter the BIOS
2. BIOS Setup :material-arrow-right: Advanced :material-arrow-right:
   CPU Power & Performance :material-arrow-right: CPU - Power Management Control
   :material-arrow-right: Config TDP Configurations :material-arrow-right:
   Change the Configurable TDP Boot Mode option

| TDP Boot Mode | Base (W) | PL1 (W) | PL2 (W) | Ratio | TAR |
| :--- | :---: | :-----: | :-----: | :---: | :-: |
| Nominal | 28W | 45W | 64W | 19 | 18  |
| Level 1 | 20W | 20W | 20W | 14 | 13  |
| Level 2 | 3W | 35W | 64W | 22 | 21  |

_(default values set in BIOS)_

- **PL:** Power Limit
- **TAR:** Turbo Activation Ratio (can be overwritten)

## Power

- **:material-usb-c-port: USB Type-C Power Delivery(PD)**
    - Power adapter provided in the box
    - UGREEN Nexode Power Bank 100W 20000mAh
      _(portable solution to have onboard the robot)_

!!! Tip

    Using a powerbank instead of using the JST PH2.0-8Pin input connector
    provides an electrically isolated power option from the robot's LiPo battery
    for powering the SBC.

## Storage

- **:fontawesome-solid-memory: Crucial P3 500 GB M.2 PCIe Gen3 NVMe SSD**
  **CT500P3SSD8** _(M.2 Key-M)_

## Display Connections

- **:material-hdmi-port: HDMI Dummy Plug**
  _(remote connection w/ graphical interface wo/ monitor)_

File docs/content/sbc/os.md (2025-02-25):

# Operating System (OS)

## Linux Distributions

The modifield Hangfa Discovery Q2 platform by INESC TEC uses the
[Robot Operating System (ROS)](https://ros.org/) set of software libraries to
facilitate the development of robot-oriented applications. As a result of using
ROS, you should take attention to the compatibility of the Linux distributions
with specific ROS versions. The following list provides a summary on the Linux
compatibility with ROS:

- [ROS 1](https://wiki.ros.org/Distributions)
    - [ROS Noetic Ninjemys](https://wiki.ros.org/noetic) _(EOL: May, 2025)_
        - Ubuntu Focal Fossa 20.04 LTS
          [[amd64]](https://releases.ubuntu.com/focal/)
          [[arm64|armhf]](https://cdimage.ubuntu.com/releases/focal/release/)
        - Debian Buster
          [[amd64|arm64]](https://www.debian.org/releases/buster/)
- [ROS 2](https://docs.ros.org/en/rolling/Releases.html)
    - [ROS 2 Foxy Fitzroy](https://docs.ros.org/en/foxy/) _(EOL: June, 2023)_
        - Ubuntu Focal Fossa 20.04 LTS
          [[amd64]](https://releases.ubuntu.com/focal/)
          [[arm64]](https://cdimage.ubuntu.com/releases/focal/release/)
    - [ROS 2 Humble Hawksbill](https://docs.ros.org/en/humble/) _(EOL: May, 2027)_
        - Ubuntu Jammy Jellyfish 22.04 LTS
          [[amd64]](https://releases.ubuntu.com/jammy/)
          [[arm64]](https://cdimage.ubuntu.com/releases/jammy/release/)
    - [ROS 2 Jazzy Jalisco](https://docs.ros.org/en/jazzy/) _(EOL: May, 2029)_
        - Ubuntu Noble Numbat 24.04 LTS
          [[amd64]](https://releases.ubuntu.com/noble/)
          [[arm64]](https://cdimage.ubuntu.com/releases/noble/release/)

Still, the remaining of the Operating System tutorial will focus on
**Ubuntu Focal Fossa 20.04 LTS** due to its compatibility with both ROS 1 and
ROS 2 versions.

## Create Bootable USB

### Rufus (Windows)

1. Download and install [Rufus](https://rufus.ie/en/)
2. Download the Ubuntu Focal Fossa 20.04 LTS image file
3. Select your :material-usb-flash-drive: USB stick for the Device option
4. Select the :material-ubuntu: Ubuntu image file for the Boot selection option
5. _(optional)_ Disable quick format and/or Enable check device for bad blocks
6. Press the Start button

### Linux

1. Open the Make Startup Disk application
2. Select the :material-ubuntu: Ubuntu image file for the CD-Drive/Image option
3. Select your :material-usb-flash-drive: USB stick for the Device option
4. Make Startup Disk

## Installation

1. :material-power: Power on or reboot the Single Board Computer (SBC)
2. Press **++del++** or **++esc++** key continuously (for LattePanda SBCs) to
   enter into BIOS menu
3. BIOS Setup :material-arrow-right: Boot :material-arrow-right: Select the
   USB drive as the first boot option
4. Save the changes and exit the boot screen
5. Select _Install Ubuntu_
6. Language
    Ubuntu Installation Welcome
7. Keyboard layout
    Ubuntu Installation Keyboard Layout
8. Select _Minimal installation_, and enable
   _Download updates while installing Ubuntu_ and
   _Install third-party software for graphics and Wi-Fi hardware_
    Ubuntu Installation Updates and other software
9. Select _Something else_ to create and resize partitions yourselft
    Ubuntu Installation Type
    - Remove all pre-existing partitions
        Ubuntu Installation Type Empty Partitions
    - SSD (`/dev/nvme0n1`)
        - 512MB EFI System Partition

            Ubuntu Installation Type EFI

        - 8192MB swap area

            Ubuntu Installation Type Swap

        - `/` root (remaining of the disk free available size)

            Ubuntu Installation Type Root

    - eMMC (`/dev/mmcblk2`)
        - `/media/data` partition

            Ubuntu Installation Type Data

        !!! Tip

            SSD is set as the boot loader and to have the OS's root partition
            due to being faster that eMMC memory. As a result, the latter can be
            used as additional data storage, following the preivous steps.

    - Final partition scheme

        Ubuntu Installation Type eMMC

        Ubuntu Installation Type SSD

    - Confirm disk changes

        

10. Timezone
    Ubuntu Installation Timezone
11. User and computer information settings
    Ubuntu Installation User and PC Information

    !!! Warning

        If you have more than 1 robot, it is advisable for you to use different
        computer's name for network discoverability purposes and alias
        definitions.

    !!! Tip

        Use user as the username for all your robots to facilite when connecting
        remotely to the robot
        (e.g., `ssh user@<robot_name>`, assuming that `<robot_name>` is defined
        as a valid network alias).

12. Press _Continue_ to finish the installation of the OS
13. Reboot the Single Board Computer (SBC)

## Setup

### Keyboard Shortcuts

1. Open Settings
    - Task Bar :material-triangle-down: :material-arrow-right:
      :material-wrench: Settings
    - Dock :material-arrow-right: :material-dots-grid: Show Applications
      :material-arrow-right: :material-wrench: Settings
2. :material-lock: Privacy :material-arrow-right: :material-lock: Screen Lock
    - Set _Blank Screen Delay_ to _Never_
    - Disable _Automatic Screen Lock_
3. :material-lightning-bolt-circle: Power
    - Set _Power Saving: Blank Screen_ to _Never_
4. :material-keyboard: Keyboard Shortcuts
    - Home folder: **++super+e++**

### File Explorer

1. Open :material-folder: File Explorer (**++super+e++**)
2. Open the :material-menu: Menu :material-arrow-right: Preferences
3. Views :material-arrow-right: Enable _List View: Allow folders to be expanded_

## Getting Started

```sh
sudo apt update
sudo apt dist-upgrade

sudo apt install build-essential git net-tools nmap terminator vim xclip
```

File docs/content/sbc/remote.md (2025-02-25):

# Remote Access

!!! Tip

    If you want to have a remote graphical output without having a monitor
    connected to the SBC (AnyDesk, RustDesk, Remmina w/ VNC),
    use the **HDMI Dummy Plug**.

## AnyDesk

1. Download AnyDesk (available at
   [https://anydesk.com/en/downloads/linux](https://anydesk.com/en/downloads/linux))
2. Execute the following commands
    ```sh
    cd ~/Downloads/
    sudo apt update
    sudo apt install ./anydesk_6.4.2-1_amd64.deb -y
    ```
3. Open AnyDesk
4. _(optional)_ Set an alias to use it for remote access instead of the
   AnyDesk ID
5. Open the :material-menu: Menu :material-arrow-right:
   :material-wrench: Settings
    - :material-lock: Security :material-arrow-right: :material-security: Unlock
        - Enable unattended access:
            - Set a password
            - Set _Full Access_ for the permission profile
        - _(optional)_ Disable _Search local network for other AnyDesk clients_
        - _(optional)_ Enable _Exclude this device from discovery_
    - _(optional)_ :fontawesome-solid-display: Display
        - Set _Best performance_ in the quality
        - Set _Optimize screen usage (strecht)_ in view mode

!!! Tip

    If you are having problems connecting to another computer through AnyDesk,
    try to remove the local cache folder.

    ```sh
    ll ~/.anydesk/
    rm -rf ~/.anydesk/
    ```

!!! Warning

    AnyDesk requires both remote access endpoints to have Internet connection.

!!! Warning

    Some IT managers may lock the remote access through AnyDesk by disabling
    connections through `*.net.anydesk.com`, even if both endpoints have an
    Internet connection.
    More information in
    [https://support.anydesk.com/knowledge/firewall](https://support.anydesk.com/knowledge/firewall).

## RustDesk

1. Download RustDesk (available at
   [https://github.com/rustdesk/rustdesk/releases/](https://github.com/rustdesk/rustdesk/releases/))
2. Execute the following commands
    ```sh
    cd ~/Downloads/
    sudo apt update
    sudo apt install ./rustdesk-1.3.7-x86_64.deb -y
    ```
3. Open RustDesk
4. Open the :material-menu: Menu :material-arrow-right:
   :material-wrench: Settings:
    - :material-lock: Security :material-arrow-right: :material-security: Unlock
      Security Settings
        - Use permanent password
        - _(optional)_ Deny LAN discovery
        - _(optional)_ Enable direct IP access :material-arrow-right: Define
          the Port (e.g., `21118`)
    - _(optional)_ :fontawesome-solid-display: Display
        - Set _Scale adaptive_
        - Set _Optimize reaction time_
        - Other default options
            - [x] Show monitors in toolbar
            - [x] Enable file copy and paste
            - [x] Use all my displays for the remote session

!!! Tip

    RustDesk is an open-source remote access software as an alternative to
    AnyDesk and similiar applications, allowing your own self-hosted servers
    and direct IP access to your machine.

!!! Warning

    Direct IP access through RustDesk remote connection is unecrypted!

## Remmina

1. Execute the following commands
    ```sh
    sudo apt install remmina remmina-plugin-rdp remmina-plugin-vnc -y
    sudo apt install vino -y
    ```
2. Open :fontawesome-solid-gear: Settings :material-arrow-right:
   :material-share-variant-outline: Sharing :material-arrow-right: Enable
   _Screen Sharing_
3. Open Remmina on the client side
4. Open a VNC connection with the address
   `<computer name>.local` or `<IP address>`

## Secure Shell (SSH)

```sh
# SBC onboard the robot
sudo apt install openssh-server

# Remote access PC
sudo apt install openssh-client

ssh user@<IP address>
```

!!! Warning

    SSH 22 default port must be open in your network's firewall settings.

## ZeroTier

1. Execute the following commands
    ```sh
    curl -s 'https://raw.githubusercontent.com/zerotier/ZeroTierOne/main/doc/contact%40zerotier.com.gpg' | gpg --import && if z=$(curl -s 'https://install.zerotier.com/' | gpg); then echo "$z" | sudo bash; fi

    sudo zerotier-cli info
    ```
2. Go to [https://my.zerotier.com/](https://my.zerotier.com/)
   :material-arrow-right: Create A Network
    - Enable _Auto-Assign from Range_ for the _IPv4 Auto-Assign_
    - Enable _Broadcast_ for _Multicast_
3. Execute the following commands
    ```sh
    sudo zerotier-cli join <Network ID>
    ```
4. Go to [https://my.zerotier.com/](https://my.zerotier.com/)
   :material-arrow-right: Access the network previously created
   :material-arrow-right: Authorize the new device
5. Execute the following commands
    ```sh
    ifconfig  # (1)!
    ```

    1. should appear a new network interface specific to ZeroTier with an
       auto-assigned **STATIC** IP address

6. Execute remote access through VNC, SSH, or another method that allows IP
   direct access **using the ZeroTier IP address**

    !!! Warning

        Both devices should be added in your private ZeroTier network

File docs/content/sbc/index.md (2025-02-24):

# Single Board Computer (SBC) Unit

The Single Board Computer (SBC) serves as the central computing unit of the
modified Hangfa Discovery Q2 platform. This computing unit is responsible for
communicating with the microcontroller via a serial port connection, executing
[Robot Operating System (ROS)](https://ros.org/)-based nodes, and interfacing
with external systems.

While Raspberry Pi SBCs could have been a more cost-effective alternative to
x86-based boards, they often face compatibility issues with certain libraries
due to their ARM architecture - a limitation shared with Jetson boards.
Additionally, Raspberry Pi boards may lack the necessary processing power for
multimodal perception applications, even when only recording data.

As a result, we opted for LattePanda SBCs, specifically, the
[LattePanda 3 Delta](https://www.lattepanda.com/lattepanda-3-delta) (used in our
experiments) and
[LattePanda Sigma](https://www.lattepanda.com/lattepanda-sigma)
(a more powerful alternative) boards. This guide provides detailed, step-by-step
instructions for intermediate and advance  on how to:

- Set up the SBCs (BIOS settings, power, storage, and display configuration)
- Install the operating system
  ([Ubuntu Focal Fossa 20.04 LTS](https://releases.ubuntu.com/focal/))
- Install and configure the ROS framework
  ([ROS 1 Noetic Ninjemys](https://wiki.ros.org/noetic) and
  [ROS 2 Foxy Fitzroy](https://docs.ros.org/en/foxy/))
- Configure remote desktop access
- Set up the development environment
- Firmware setup in terms of udev rules for peripheral management, and
  installation and configuration of the advanced serial monitor application
  [CoolTerm](https://freeware.the-meiers.org/)

Following these step-by-step instructions will ensure that you are capable of
replicating our configuration in terms of computing unit, while may also give
you additional ideas on how to improve it even further.

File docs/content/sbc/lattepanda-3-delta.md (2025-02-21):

# LattePanda 3 Delta

## Links

- [LattePanda 3 Delta](https://www.lattepanda.com/lattepanda-3-delta)
- [LattePanda 3 Delta Specification](https://docs.lattepanda.com/content/3rd_delta_edition/specification/)
- [Pinout and Hardware Diagram](https://docs.lattepanda.com/content/3rd_delta_edition/io_playability/)
- [Initial Setup of the 3 Delta by LattePanda](https://docs.lattepanda.com/content/3rd_delta_edition/get_started/)
- [LattePanda 3 Delta 3D Model](https://github.com/LattePandaTeam/LattePanda-3D-Models/tree/master/LattePanda%203%20Delta)

## Specifications

| Content | Specs. |
| --- | --- |
| Processor | Intel® Celeron® Processor N5105 (Frequency: 2.00GHz ~ 2.90GHz) |
| Graphics | Intel® UHD Graphics (Frequency: 450MHz ~ 800MHz) |
| Memory | 8GB LPDDR4 2933MHz |
| Storage | 64GB eMMC V5.1 |
| Wireless | Intel® AX201 WiFi 6 (802.11ax), 2.4GHz and 5GHz (160MHz) Supported; Bluetooth® 5.2 |
| Ethernet | Intel® I211-AT / I225-V PCIe Gigabit LAN, Wake-On-LAN Supported |
| Video | HDMI 2.0b; DP 1.4 via USB Type-C; eDP 30Pin (two lanes) |
| Audio | Microphone + Headphone Combo Connector |
| USB | 1x USB 3.2 gen 2 Type-A; 2x USB 3.2 gen1 Type-A; 1x USB 2.0 Type-C |
| Expansion Slots | M.2 Key B(2242/2252/2280): SATA III, USB2.0, USB3.0, SIM; M.2 Key M(2280): PCIe 3.0 x2; Micro-SD + Micro-SIM Combo Card Connector |
| Coprocessor | Microchip® ATmega32U4-MU |
| GPIO Female Headers | Atmega32U4 Pinout; BIOS Flash Pinout; 5V & 3.3V Output; 12V DC Input; USB 2.0; RS232; Audio; Status Control & Indication |
| TPM | Built-in TPM (2.0) |
| BIOS Function | Auto Power On, Watchdog Timer, Serial Port Redirection, etc. |
| Power | PH2.0-4Pin DC Input: 12V; USB Type-C PD Input: 15V DC |
| RTC | CR927 3V |
| Dimension | 125mm x 78mm x16mm |
| Default Built-in OS | Windows 10 Pro 21H2; Windows 10 IoT Enterprise 2021 LTSC |
| Compatible OS | Windows 10, Windows 11, Ubuntu |
| Environment | Operating Temperature: 0~60℃; Relative Humidity: 0%~80% |
| Certification | CE, FCC, KC, RoHS |

## Initial Setup

**Preparations**

- :material-cable-data:         HDMI Cable
- :material-monitor:            External HDMI Monitor
- :material-keyboard:           Keyboard and a Mouse
- :material-power-plug-battery: Power Adapter
- :material-antenna:            Pair of WIFI/BT antennas
    - Antennas that come in the box
    - Bingfu Antena WiFi Dual Band RP-SMA 25cm U.FL IPX IPEX MHF4 M.2 NGFF Intel

!!! Warning "WiFi Antenna Interface"

    WiFi card on the LattePanda 3 Delta is not a traditional one as
    you see in desktops (the connector is different: IPEX4 2.4 & 5G Dual-band).

**Instructions**

1. Attach the Wi-Fi/BT antennas to the sockets
2. Connect an HDMI display
3. Connect the keyboard and mouse to the LattePanda 3 Delta
4. Connect the power adapter provided in the SBC's box
5. Press the power button and the blue LED indicator will light up
    - Default OS is Windows 10 :fontawesome-brands-windows:

## BIOS Setup

### Entering BIOS

**Default**

1. Power on or reboot LattePanda
2. Press **++del++** or **++esc++** key continuously to
   enter into BIOS menu before you see the LattePanda logo on the splash screen

**Windows 10**

1. Start Menu :fontawesome-brands-windows: :material-arrow-right:
   Press **++shift++** + Restart
2. Choose :material-tools: Troubleshoot :material-arrow-right: Advanced Options
   :material-arrow-right: UEFI Firmware Settings :material-arrow-right:
   Restart

### Auto Power-on

1. Power on the LattePanda and enter the BIOS
2. BIOS Setup :material-arrow-right: Advanced :material-arrow-right:
   Power Management :material-arrow-right: ACPowerLoss :material-arrow-right:
   Set the ACPowerLoss option to `PowerOn`
3. Save & Exit (Press **++f4++**)

## Power

- **:material-usb-c-port: USB Type-C Power Delivery(PD)**
    - Power adapter provided in the box
    - Powerbank Xiaomi Mi 50W 20000mAh _(portable solution to have onboard the_
      _robot)_

!!! Tip

    Using a powerbank instead of using the JST PH2.0-4Pin input connector
    provides an electrically isolated power option from the robot's LiPo battery
    for powering the SBC.

## Storage

- **:material-memory: 64GB eMMC V5.1** _(internal)_
- **:fontawesome-solid-memory: Crucial P3 500 GB M.2 PCIe Gen3 NVMe SSD**
  **CT500P3SSD8** _(M.2 Key-M)_

## Display Connections

- **:material-hdmi-port: HDMI Dummy Plug**
  _(remote connection w/ graphical interface wo/ monitor)_

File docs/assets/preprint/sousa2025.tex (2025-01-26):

\documentclass[letterpaper,10pt,conference]{IEEEtran} % Comment if a4paper
% \documentclass[a4paper,10pt,conference]{IEEEtran}   % Uncomment for a4 paper
\IEEEoverridecommandlockouts                          % Only needed if you want to use the \thanks command (funding)

% TEMPLATE VERSION DATA: 27/06/2024

\usepackage{cite}     % compressed, sorted lists of numerical citations
\usepackage{hyperref} % cross-referencing to generate hyperlints in the document
\usepackage{amsmath}  % enhanced functions to improve math content display
\usepackage{amssymb}  % math symbols
\usepackage{amsfonts} % math extended fonts
\usepackage{graphicx} % enhanced support for graphics display
\usepackage[font=small]{caption}
\usepackage[font=footnotesize]{subcaption}
\usepackage{algorithmicx}         % pseudocode environments
\usepackage[noend]{algpseudocode}
\usepackage{enumitem} % control layout of itemize, enumerate, description
\usepackage{svg}      % include svg graphics
\usepackage{textcomp} % additional text symbols (e.g., bullet, copyright, ...)
\usepackage{xcolor}   % color extensions

% \usepackage[backend=biber,
%             %style=apa,
%             %style=numeric,
%             style=numeric-comp,
%             bibstyle=numeric,
%             %citestyle=authoryear-comp,
%             citestyle=numeric-comp,
%             %sorting=nyt,
%             sorting=none,
%             maxnames=8,
%             minnames=3
%             %maxcitenames=2,
%             %mincitenames=1
%             ]{biblatex}

%% Style hacks to save space
% \setlength{\textfloatsep}{1.5em}
% \setlength{\dbltextfloatsep}{1.5em}

%% Key definitions for text elements.
\def\secref#1{Section~\ref{#1}}
\def\figref#1{Fig.~\ref{#1}}
\def\tabref#1{Table~\ref{#1}}
\def\eqref#1{Equation~(\ref{#1})}
\def\algref#1{Algorithm~\ref{#1}}

%% Other useful macros
\newcommand\todo[1]{\textbf{[TODO: #1}]}
\newcommand\etal{\emph{et~al.}}

%% Some math definition
\def\argmax{\mathop{\rm argmax}}
\def\argmin{\mathop{\rm argmin}}
\newcommand{\bigO}[1]{$\mathcal{O}(#1)$}

\thispagestyle{empty}
\pagestyle{empty}

%% Bibliography (biblatex)
% \addbibresource{references.bib}
% \renewcommand*{\bibfont}{\normalfont\small}

%%%%%%%%%%%%%%%%%%%%%%%%%%%%%%%%%%%%%%%%%%%%%%%%%%%%%%%%%%%%%%%%%%%%%%%%%%%%%%%%

\def\finalversion{}
% \let\finalversion\undefined

%%%%%%%%%%%%%%%%%%%%%%%%%%%%%%%%%%%%%%%%%%%%%%%%%%%%%%%%%%%%%%%%%%%%%%%%%%%%%%%%

\begin{document}

\bstctlcite{IEEEexample:BSTcontrol}
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

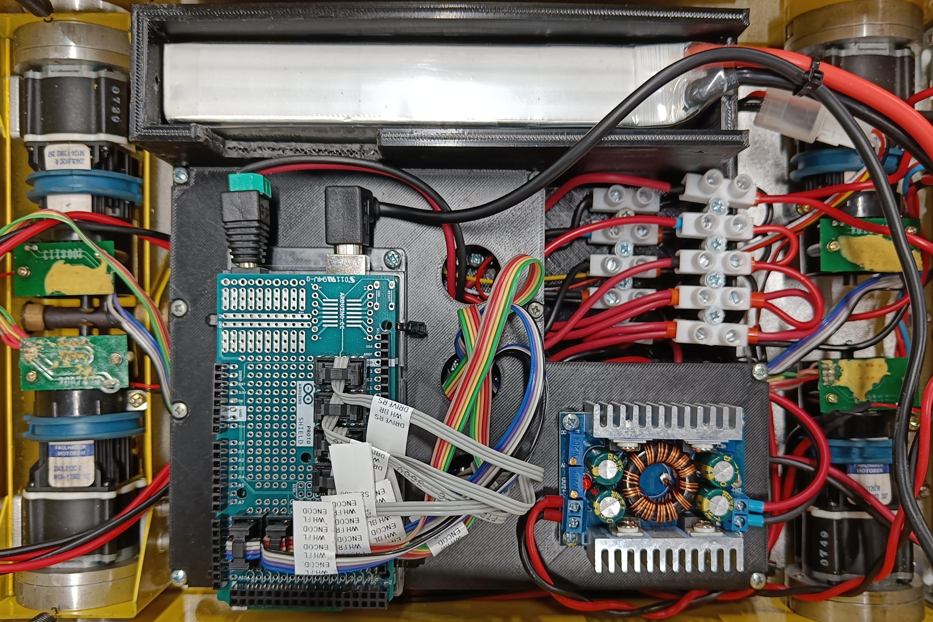
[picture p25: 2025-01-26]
docs/assets/preprint/figs/electronics_3d-framework_1st-level.jpg

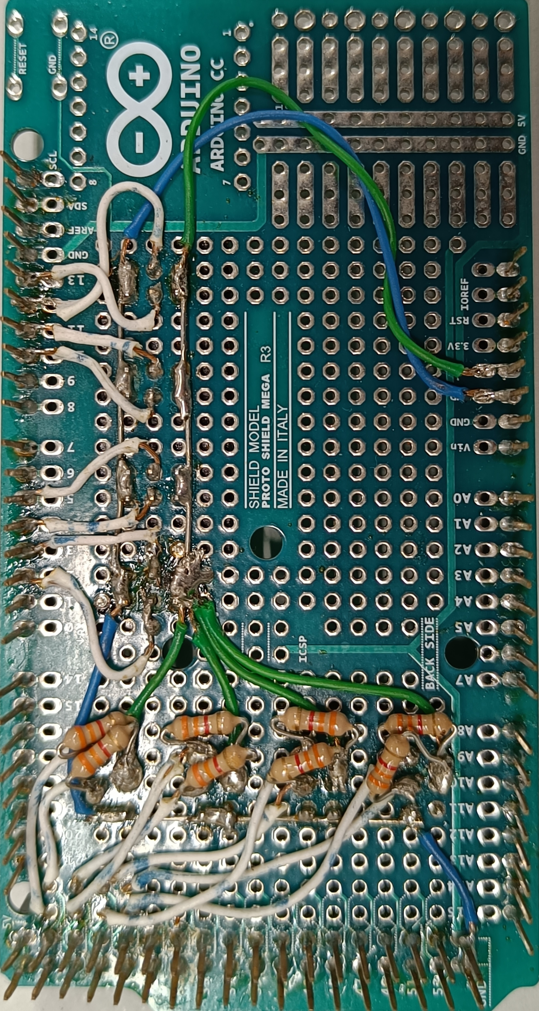
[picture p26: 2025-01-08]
docs/assets/electronics/electronics_arduino-mega-proto-shield_back.jpg

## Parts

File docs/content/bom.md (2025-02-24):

# Bill Of Materials (BOM)

<div>
  <object data="../../assets/bom/bom.pdf" width="100%" type="application/pdf"
          style="aspect-ratio:297/210;">
    <p>This browser does not support PDF! Click
    <a href="../../assets/bom/bom.pdf">here</a> to download the file.</p>
  </object>
</div>

## Documents

- [bom.pdf](../assets/bom/bom.pdf)
- [bom.xlsx](../assets/bom/bom.xlsx)

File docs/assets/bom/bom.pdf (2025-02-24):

supplier 1 | supplier 2 | supplier 3 | (supplier alternativesfocused on the Portuguese market) Scroll to see the links | referenceID | #un. url | comments | url | €/un. | € | url | €/un. | € | url | €/un. | € | (!!!always check different supplier alternatives for the same product / item!!!) Original HangfaDiscovery Q2 DiscoveryQ2 | DQ2 | 1 hangfa | only used the mechanical parts of the robot, all the electronics were rebuilt | hangfa-eu | N/A | N/A | ozrobotics | $ 1,629.00 $ 1,629.00 | hangfa-cn | N/A | N/A DC Motor Drivers Cytron 13A 5-30V Single DC Motor Driver | MD10CR3 | 4 cytron | (preferred)10A should be more than ok for the motors, single

channel facilitates the replacementof possible failed drivers

robotshop (https://eu.robotshop.com/products/cytron-13a-5-30v-single-dc-motor-controller) | € | 18.88 € | 75.52 | botland (https://botland.store/motor-drivers-modules/12397-cytron-md10c-single-channel-30v-13a-motor-controller-5904422340995.html) | € | 14.90 € | 59.60 | opencircuit (https://opencircuit.shop/product/10amp-5v-30v-dc-motor-driver) | € | 19.95 € | 79.80 Cytron 10A 5-30V Dual DC MotorDriver | MDD10A | 2 cytron | (preferred alternative)dual channel drivers shouldbe more

cheap (only two required)

robotshop (https://eu.robotshop.com/products/cytron-10a-5-30v-dual-channel-dc-motor-driver) | € | 27.80 € | 55.60 | botland (https://botland.store/drivers-for-dc-motors/15818-cytron-mdd10a-dual-channel-30v-10a-motor-controller-5904422350444.html) | € | 26.50 € | 53.00 | opencircuit (https://opencircuit.shop/product/10amp-5v-30v-dc-motor-driver-2-channels) | € | 32.95 € | 65.90 Cytron 20A 6-30V Single DC Motor Driver | MD20A | 4 cytron | - | robotshop | € | 24.83 € | 99.32 | botland | € | 22.90 € | 91.60 | opencircuit | € | 29.35 € | 117.40 Cytron 20A 6-30V Dual DC MotorDriver | MDD20A | 2 cytron | - | robotshop | € | 41.39 € | 82.78 | botland | € | 38.50 € | 77.00 | opencircuit | € | 43.70 € | 87.40 ElectronicsBattery Tattu 10000mAh11.1V 15C 3S LiPo | TAA10K3S15E5 | 1 gensace | (preferred)max. continuousdischarge of 150A and a

10000mAhcapacity should be appropriatefor more than 1h of continuoususage of the platform (accounting for sensors and

other electronicdevices) | gensace (https://gensace.de/products/tattu-11-1v-15c-3s-10000mah-lipo-battery-pack) | € | 103.36 € | 103.36 | mercadorc (https://www.mercadorc.es/Tattu-111V-15C-3S-10000mAh-Lipo-Battery-Pack/en) | € | 104.00 € | 104.00 | rcinnovations (https://rc-innovations.es/en/shop/6928493302149-tattu-10000mah-11-1v-3s-15c-lipo-battery-7718) € | 93.99 € | 93.99 Tattu 8000mAh11.1V 15C 3S1PLipo | TAA80003S15E5 | 1 gensace (https://gensace.de/products/tattu-8000mah-11-1v-15c-3s1p-lipo-battery-pack-with-ec5-plug) | - | gensace (https://gensace.de/products/tattu-8000mah-11-1v-15c-3s1p-lipo-battery-pack-with-ec5-plug) | € | 93.01 € | 93.01 | mercadorc (https://www.mercadorc.es/TATTU-8000mAh-111V-15/30C-3S1P-Lipo-Battery-Pack) | € | 88.00 € | 88.00 | rcinnovations (https://rc-innovations.es/en/shop/6928493302125-tattu-8000mah-11-1v-3s-15c-lipo-battery-7720) € | 85.99 € | 85.99 Gens ace 8000mAh11.1V 100C3S Lipo | GEA8K3S100E5 | 1 gensace | - | gensace | € | 72.35 € | 72.35 | smartmodelism€ | 74.94 € | 74.94 | rcparts | € | 79.30 € | 79.30 ElectronicsBattery ManagementSystem (BMS) Passive
18650 BMS Charger 3S 12.6V 20A Rev. 2.0 | - | 1 botnroll (https://www.botnroll.com/en/bms/2558-li-ion-18650-bms-charger-pcb-prot-board-3s-12-6v-20a.html) | (preferred)peak currentof 20A and continuous output of 10A, ok for the elctronics part; if you power the SBC to the

electronics battery, probablygo for the 40A BMS

botnroll (https://www.botnroll.com/en/bms/2558-li-ion-18650-bms-charger-pcb-prot-board-3s-12-6v-20a.html) | € | 5.50 € | 5.50 | ptrobotics (https://www.ptrobotics.com/baterias-litium/7231-18650-lithium-battery-bms-protection-board-3s-126v-20a.html) | € | 5.04 € | 5.04 | aliexpress (https://pt.aliexpress.com/i/32809110553.html) | € | 0.49 € | 0.49
18650 BMS Charger 3S 11.1~12.6V40A | - | 1 botnroll (https://www.botnroll.com/en/bms/4974-li-ion-18650-bms-charger-pcb-prot-board-3s-11-1v-12-6v-40a-with-balance.html) | - | botnroll (https://www.botnroll.com/en/bms/4974-li-ion-18650-bms-charger-pcb-prot-board-3s-11-1v-12-6v-40a-with-balance.html) | € | 4.90 € | 4.90 | ptrobotics (https://www.ptrobotics.com/el-wire-fio-electroiluminescente/7232-18650-lithium-battery-bms-protection-board-3s-111v-126v-40a.html) | € | 6.64 € | 6.64 | aliexpress (https://pt.aliexpress.com/item/32835818466.html) | € | 3.69 € | 3.69 DC/DC Buck BoostConverter(optional:only requiredto ensureDC regulated powerto the 2D/3DLiDARs, ethernet switch and/or powerthe SBC) DC 5-30V to 1.25-30V 8A Buck Boost Converter | - | 1 aliexpress | (optional) | aliexpress | € | 14.05 € | 14.05 | aliexpress | € | 5.10 € | 5.10 | - | - | - MicrocontrollerBoard Circuit Arduino Mega 2560 Rev3 | A000067 | 1 arduino | (required) | arduino | € | 51.62 € | 51.62 | robertmauser € | 42.90 € | 42.90 | botnroll | € | 42.90 € | 42.90 Arduino Mega Proto Shield Rev3 (PCB) | A000080 | 1 arduino | (required) | arduino | € | 6.35 € | 6.35 | robertmauser € | 6.40 € | 6.40 | opencircuit | € | 5.90 € | 5.90 Female header stackable8 pin (10 un.) | - | 1 opencircuit | (optional) allows to stack protoboard circuitson top of Arduino Mega and/or helps to have easy accessabilityto PWM and

encoders signalsusing an oscilloscope

opencircuit (https://opencircuit.pt/product/female-header-stackable-8-pin) | € | 3.05 € | 3.05 | - | - | - | - | - | - Female header stackable10 pin (10 un.) | - | 1 opencircuit | opencircuit | € | 3.50 € | 3.50 | - | - | - | - | - | - Female header stackable2x18 pin (2 un.) | - | 1 opencircuit | opencircuit | € | 3.20 € | 3.20 | - | - | - | - | - | -
IDC HeaderStraight 6-Way | - | 8 - | (optional) although we used IDC connectors to make it compatiblewith the originalcables, you may use other
robertmauser (https://mauser.pt/catalog/product_info.php?products_id=011-0800) € | 0.45 € | 3.60 | rs (https://pt.rs-online.com/web/p/conectores-macho-para-pcb/8323496) | € | 0.66 € | 5.28 | ptrobotics (https://www.ptrobotics.com/idc/4469-idc-header-straight-6way.html) | € | 0.25 € | 2.00
IDC Socket 6-Way | - | 8 - | robertmauser (https://mauser.pt/catalog/product_info.php?products_id=011-0827) € | 0.53 € | 4.24 | rs (https://pt.rs-online.com/web/p/conectores-idc/8323648) | € | 1.09 € | 8.72 | ptrobotics (https://www.ptrobotics.com/idc/957-idc-socket-6way.html) | € | 0.49 € | 3.92 SingleBoard Computer(SBC) LattePanda3 Delta | DFR0981 | 1 lattepanda | - | farnell | € | 220.62 € | 220.62 | digikey | € | 265.66 € | 265.66 | mouser | € | 265.05 € | 265.05 Samsung 970 EVOPlus 250 GB PCIe NVMe M.2 | MZ-V7S250BW | 1 samsung | (optional)if you want to upgradethe 64GB storage (faster read
and writing speeds, 64BG for data e.g.) | amazon-es (https://www.amazon.es/dp/B07MHXYL6T) | € | 48.21 € | 48.21 | kuantokusta (https://www.kuantokusta.pt/p/240736/samsung-250gb-970-evo-plus-nvme-m2-mz-v7s250bw) | € | 51.54 € | 51.54 | - | - | - UGREENUSB 3.0 Hub with 4-Port | CM21950985 | 1 ugreen (https://eu.ugreen.com/products/ugreen-usb-hub-3-0-ultra-slim-4-port-usb-3-hub-with-5gbps-data-transfer) | (optional)increases#USB ports available(e.g., joystick, keyboard and/ormouse adapter,etc.) | amazon-es (https://www.amazon.es/-/pt/dp/B0CD1BHXPZ) | € | 12.19 € | 12.19 | kuantokusta (https://www.kuantokusta.pt/p/10379518/ugreen-hub-usb-4-portas-usb-30-cinza) | - | - | - | - | - SingleBoard Computer(SBC) Battery (optional:power SBC throughUSB C PD protocol;if not used, DC/DC buck-boost converterto have 11-15VDC) PowerbankXiaomi Mi 50W 20000 mAh | PB200SZM | 1 xiaomi | (preferred)50W > minimum 24W, if 3A current consumption

the 20000mAhallows for 6h+

amazon-es (https://www.amazon.es/-/pt/dp/B0BFBBQQXK) | € | 80.17 € | 80.17 | kuantokusta (https://www.kuantokusta.pt/p/7781139/xiaomi-mi-50w-20000-mah-black) | € | 50.46 € | 50.46 | - | - | - UGREENNexodePowerbank100W 20000mAh | - | 1 ugreen | (not tested!) | amazon-es | € | 81.32 € | 81.32 | ugreen | € | 69.99 € | 69.99 | - | - | - Networking(optional:defaultnetwork interfacesof the SBC may be ok for you) Bingfu AntenaWiFi Dual Band RP-SMA 25cm U.FL IPX IPEX MHF4 M.2 NGFFIntel | BFN00525 | 1 bingfu | (optional) same Wi-Fi antennasas in F1TENTH | amazon-es | € | 12.19 € | 12.19 | - | - | - | - | - | - Brainboxes5 Port UnmanagedEthernetSwitch 10/100Mbps | SW-005 | 1 brainboxes | (optional)if you want to have multiple 2D/3D LiDARs

communicatingto the SBC (single ethernetport…)

farnell (https://pt.farnell.com/brainboxes/sw-005/switch-n-w-5port-100mbps-din-rail/dp/2383213) | € | 61.30 € | 61.30 | digikey (https://www.digikey.pt/pt/products/detail/brainboxes/SW-005/10707220) | € | 48.41 € | 48.41 | mouser (https://pt.mouser.com/ProductDetail/Brainboxes/SW-005?qs=BJlw7L4Cy7944%2FIWYfp8eA%3D%3D) | € | 48.30 € | 48.30 Brainboxes5 Port UnmanagedEthernetSwitch 10/100/1000Mbs | SW-015 | 1 brainboxes | (optional) some 3D LiDAR may surpass the 100Mbps

requirement(dependingon the configuration)

farnell (https://pt.farnell.com/brainboxes/sw-015/ernet-switch-unmanaged-gigabit/dp/3604249) | € | 102.29 € | 102.29 | digikey (https://www.digikey.pt/pt/products/detail/brainboxes/SW-015/13152346) | € | 95.04 € | 95.04 | mouser (https://pt.mouser.com/ProductDetail/Brainboxes/SW-015?qs=W%2FMpXkg%252BdQ6e4NboBK2WDQ%3D%3D) | € | 87.12 € | 87.12 UGREENRJ45 female couplerGigabitEthernet 1000Mbps | NW114 20390 | 1 ugreen | (optional)facilitates the connectionof the Hokuyo UST-10LX
(short Ethernet cable) | amazon-es (https://www.amazon.es/-/pt/dp/B016B13U5S) | € | 3.66 € | 3.66 | kuantokusta (https://www.kuantokusta.pt/p/7909830/ugreen-extensao-nw114-uniao-rj45-preta?sort=5) | € | 3.90 € | 3.90 | - | - | - Miscellaneous XT30 Connector- Pair Male/Female | xt30 | 10 - | (optional) DC derivation bus to powerthe sensors | botnroll | € | 1.50 € | 15.00 | digikey | € | 1.81 € | 18.10 | aliexpress | € | 0.26 € | 2.60 XT60 Connector- Pair Male/Female | xt60 | 5

(optional) connectionfrom the inside to the exterior of the

original DiscoveryQ2 metallicbox | botnroll (https://www.botnroll.com/en/xt-t-deans/219-prt-10474-conector-xt60-macho-e-femea.html) | € | 1.50 € | 7.50 | digikey (https://www.digikey.pt/pt/products/detail/dfrobot/FIT0587/9559256) | € | 1.43 € | 7.15 | aliexpress (https://www.aliexpress.us/item/3256806917123984.html) | € | 0.21 € | 1.05 TerminalBlocks 10mm² VDE DIN EN 60998 - DIN EN 60999 | 096-9065 | 2 robertmauser (https://mauser.pt/catalog/product_info.php?products_id=096-9065) GND and Vcc (Vbattery or Vbms) buses | robertmauser (https://mauser.pt/catalog/product_info.php?products_id=096-9065) € | 2.17 € | 4.34 | - | - | - | - | - | - Sensors

(dependson your desired perception system! Here only put the ones tested with the modified platform)

Inertial MeasurementUnits (IMUs) Xsens MTi-3 AHRS | MTi-3-5A-DK | 1 xsens (https://www.movella.com/products/sensor-modules/xsens-mti-3-ahrs) | - | mouser (https://pt.mouser.com/ProductDetail/Movella-Xsens/MTi-3-5A-DK?qs=9vOqFld9vZVm8SUT4T13Og%3D%3D) | € | 458.85 € | 458.85 | digikey (https://www.digikey.pt/pt/products/detail/xsens-a-movella-brand/MTI-3-5A-DK/18718047) | € | 427.54 € | 427.54 | farnell (https://pt.farnell.com/xsens/mti-3-0i-dk/dev-kit-3-axis-accel-gyro-magnetometer/dp/3793984) | € | 419.99 € | 419.99 Xsens MTi-630 AHRS | MTi-630-DK | 1 xsens | - | mouser | € 1,054.50 € 1,054.50 | digikey | € 1,086.38 € 1,086.38 | farnell | € 1,034.00 € 1,034.00
2D Laser Scanners Hokuyo UST-10LX-H01/H02 | UST-10LX | 1 hokuyo-usa (https://hokuyo-usa.com/products/lidar-obstacle-detection/ust-10lx) | - | robotshop (https://eu.robotshop.com/products/hokuyo-ust-10lx-scanning-laser-rangefinder-eu) | € 1,783.50 € 1,783.50 | generationrobo€ (https://www.generationrobots.com/en/401755-hokuyo-ust-10lx-scanning-laser-range-finder.html) 1,878.00 € 1,878.00 | - | - | - LDRobot D300Kit LD-19 | D300 | 1 ldrobot | - | robotshop | € | 121.77 € | 121.77 | amazon-es | € | 60.98 € | 60.98 | dfrobot | $ | 119.00 $ | 119.00 SLAMTECRPLIDAR S2 | S2 | 1 slamtec | - | robotshop | € | 471.88 € | 471.88 | generationrobo€ | 536.64 € | 536.64 | amazon-es | € | 405.59 € | 405.59 YDLIDAR X4 | X4 | 1 ydlidar | - | xiaor-geek | $ | 96.99 $ | 96.99 | rlx | € | 128.17 € | 128.17 | - | - | - 3D Light DetectionAnd Ranging (LiDAR) Livox Mid-360 | mid-360 | 1 livox | - | livox | € | 659.00 € | 659.00 | - | - | - | - | - | - OusterOS1 64 | os1-64 | 1 ouster | - | - | - | - | - | - | - | - | - | - RoboSenseRS-HELIOS-5515 | rs-helios-5515 | 1 robosense | - | robotshop | € 5,166.00 € 5,166.00 | generationrobo€ 4,742.40 € 4,742.40 | - | - | - VelodyneVLP-16 | vlp-16 | 1 ouster | - | - | - | - | - | - | - | - | - | - RGB + DepthCameras
Intel RealSense D455 | d455 | 1 intel (https://www.intelrealsense.com/depth-camera-d455/) | - | mouser (https://pt.mouser.com/ProductDetail/Intel/82635DSD455?qs=sPbYRqrBIVkW8YqcWqMK9g%3D%3D) | € | 439.66 € | 439.66 | digikey (https://www.digikey.pt/pt/products/detail/intel-realsense/82635DSD455/12429610) | € | 423.73 € | 423.73 | rs (https://pt.rs-online.com/web/p/camaras-de-profundidad/2026353) | € | 676.78 € | 676.78
Intel RealSense L515 | l515 | 1 intel (https://www.intelrealsense.com/lidar-camera-l515/) | - | digikey (https://www.digikey.pt/pt/products/detail/intel-realsense/82638L515G1PRQ/11688015) | € | 595.13 € | 595.13 | - | - | - | - | - | - OAK-D Pro Fixed Focus | A00565 | 1 luxonis | - | luxonis | $ | 349.00 $ | 349.00 | mouser | € | 331.55 € | 331.55 | digikey | € | 490.82 € | 490.82

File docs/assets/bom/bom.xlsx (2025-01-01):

 |  |  |  |  | supplier 1 |  |  | supplier 2 |  |  | supplier 3 |  |  | (supplier alternatives focused on the Portuguese market)
Scroll to see the links | reference ID | #un. | url | comments | url | €/un. | € | url | €/un. | € | url | €/un. | € | (!!!always check different supplier alternatives for the same product / item!!!)
Original Hangfa Discovery Q2
Discovery Q2 | DQ2 | 1 | hangfa (https://www.hangfa-europe.com/en/omni-robot/discovery/discoveryq2) | only used the mechanical parts of the robot, all the electronics were rebuilt | hangfa-eu (https://www.hangfa-europe.com/en/omni-robot/discovery/discoveryq2) | N/A | N/A | ozrobotics (https://ozrobotics.com/shop/discovery-q2-robot-platform/) | $1629.00 | $1629.00 | hangfa-cn (http://www.cdhfyy.com/EN/robot/DiscoveryQ2.html) | N/A | N/A
DC Motor Drivers
Cytron 13A 5-30V Single DC Motor Driver | MD10C R3 | 4 | cytron (https://www.cytron.io/p-10amp-5v-30v-dc-motor-driver) | (preferred) 10A should be more than ok for the motors, single channel facilitates the replacement of possible failed drivers | robotshop (https://eu.robotshop.com/products/cytron-13a-5-30v-single-dc-motor-controller) | €18.88 | €75.52 | botland (https://botland.store/motor-drivers-modules/12397-cytron-md10c-single-channel-30v-13a-motor-controller-5904422340995.html) | €14.90 | €59.60 | opencircuit (https://opencircuit.shop/product/10amp-5v-30v-dc-motor-driver) | €19.95 | €79.80
Cytron 10A 5-30V Dual DC Motor Driver | MDD10A | 2 | cytron (https://www.cytron.io/p-10amp-5v-30v-dc-motor-driver-2-channels) | (preferred alternative) dual channel drivers should be more cheap (only two required) | robotshop (https://eu.robotshop.com/products/cytron-10a-5-30v-dual-channel-dc-motor-driver) | €27.80 | €55.60 | botland (https://botland.store/drivers-for-dc-motors/15818-cytron-mdd10a-dual-channel-30v-10a-motor-controller-5904422350444.html) | €26.50 | €53.00 | opencircuit (https://opencircuit.shop/product/10amp-5v-30v-dc-motor-driver-2-channels) | €32.95 | €65.90
Cytron 20A 6-30V Single DC Motor Driver | MD20A | 4 | cytron (https://www.cytron.io/p-20amp-6v-30v-dc-motor-driver) | - | robotshop (https://eu.robotshop.com/products/cytron-20a-6-30v-single-dc-motor-controller) | €24.83 | €99.32 | botland (https://botland.store/motor-drivers-modules/14000-cytron-md20a-single-channel-motor-controller-30v20a-5904422342326.html) | €22.90 | €91.60 | opencircuit (https://opencircuit.shop/product/20amp-6v-30v-dc-motor-driver) | €29.35 | €117.40
Cytron 20A 6-30V Dual DC Motor Driver | MDD20A | 2 | cytron (https://www.cytron.io/p-20amp-6v-30v-dc-motor-driver) | - | robotshop (https://eu.robotshop.com/products/cytron-20a-6v-30v-dual-dc-motor-driver) | €41.39 | €82.78 | botland (https://botland.store/motor-drivers-modules/18881-cytron-mdd20a-two-channel-motor-driver-30v20a-5904422384180.html) | €38.50 | €77.00 | opencircuit (https://opencircuit.pt/product/20amp-6v-30v-dc-motor-driver-2-channels) | €43.70 | €87.40
Electronics Battery
Tattu 10000mAh 11.1V 15C 3S LiPo | TAA10K3S15E5 | 1 | gensace (https://gensace.de/products/tattu-11-1v-15c-3s-10000mah-lipo-battery-pack) | (preferred) max. continuous discharge of 150A and a 10000mAh capacity should be appropriate for more than 1h of continuous usage of the platform (accounting for sensors and other electronic devices) | gensace (https://gensace.de/products/tattu-11-1v-15c-3s-10000mah-lipo-battery-pack) | €103.36 | €103.36 | mercadorc (https://www.mercadorc.es/Tattu-111V-15C-3S-10000mAh-Lipo-Battery-Pack/en) | €104.00 | €104.00 | rcinnovations (https://rc-innovations.es/en/shop/6928493302149-tattu-10000mah-11-1v-3s-15c-lipo-battery-7718) | €93.99 | €93.99
Tattu 8000mAh 11.1V 15C 3S1P Lipo | TAA80003S15E5 | 1 | gensace (https://gensace.de/products/tattu-8000mah-11-1v-15c-3s1p-lipo-battery-pack-with-ec5-plug) | - | gensace (https://gensace.de/products/tattu-8000mah-11-1v-15c-3s1p-lipo-battery-pack-with-ec5-plug) | €93.01 | €93.01 | mercadorc (https://www.mercadorc.es/TATTU-8000mAh-111V-15/30C-3S1P-Lipo-Battery-Pack) | €88.00 | €88.00 | rcinnovations (https://rc-innovations.es/en/shop/6928493302125-tattu-8000mah-11-1v-3s-15c-lipo-battery-7720) | €85.99 | €85.99
Gens ace 8000mAh 11.1V 100C 3S Lipo | GEA8K3S100E5 | 1 | gensace (https://gensace.de/products/gens-ace-8000mah-11-1v-100c-3s1p-lipo-battery-pack-with-ec5-bashing-series) | - | gensace (https://gensace.de/products/gens-ace-8000mah-11-1v-100c-3s1p-lipo-battery-pack-with-ec5-bashing-series) | €72.35 | €72.35 | smartmodelismo (https://smartmodelismo.pt/produto/bateria-8000mah-11-1v-100c-lipo-3s-pack-ec5-plug-bashing-series-gens-ace/) | €74.94 | €74.94 | rcparts (http://www.rcparts.eu/8000mah-gens-ace-bashing-100c-11.1v-lipo-battery-pack.html) | €79.30 | €79.30
Electronics Battery Management System (BMS) Passive
18650 BMS Charger 3S 12.6V 20A Rev. 2.0 | - | 1 | botnroll (https://www.botnroll.com/en/bms/2558-li-ion-18650-bms-charger-pcb-prot-board-3s-12-6v-20a.html) | (preferred) peak current of 20A and continuous output of 10A, ok for the elctronics part; if you power the SBC to the electronics battery, probably go for the 40A BMS | botnroll (https://www.botnroll.com/en/bms/2558-li-ion-18650-bms-charger-pcb-prot-board-3s-12-6v-20a.html) | €5.50 | €5.50 | ptrobotics (https://www.ptrobotics.com/baterias-litium/7231-18650-lithium-battery-bms-protection-board-3s-126v-20a.html) | €5.04 | €5.04 | aliexpress (https://pt.aliexpress.com/i/32809110553.html) | €0.49 | €0.49
18650 BMS Charger 3S 11.1~12.6V 40A | - | 1 | botnroll (https://www.botnroll.com/en/bms/4974-li-ion-18650-bms-charger-pcb-prot-board-3s-11-1v-12-6v-40a-with-balance.html) | - | botnroll (https://www.botnroll.com/en/bms/4974-li-ion-18650-bms-charger-pcb-prot-board-3s-11-1v-12-6v-40a-with-balance.html) | €4.90 | €4.90 | ptrobotics (https://www.ptrobotics.com/el-wire-fio-electroiluminescente/7232-18650-lithium-battery-bms-protection-board-3s-111v-126v-40a.html) | €6.64 | €6.64 | aliexpress (https://pt.aliexpress.com/item/32835818466.html) | €3.69 | €3.69
DC/DC Buck Boost Converter (optional: only required to ensure DC regulated power to the 2D/3D LiDARs, ethernet switch and/or power the SBC)
DC 5-30V to 1.25-30V 8A Buck Boost Converter | - | 1 | aliexpress (https://www.aliexpress.us/item/3256806821997580.html) | (optional) | aliexpress (https://www.aliexpress.us/item/3256806821997580.html) | €14.05 | €14.05 | aliexpress (https://www.aliexpress.us/item/3256804373833556.html) | €5.10 | €5.10 | - | - | -
Microcontroller Board Circuit
Arduino Mega 2560 Rev3 | A000067 | 1 | arduino (https://store.arduino.cc/en-pt/products/arduino-mega-2560-rev3) | (required) | arduino (https://store.arduino.cc/en-pt/products/arduino-mega-2560-rev3) | €51.62 | €51.62 | robertmauser (https://mauser.pt/catalog/product_info.php?products_id=096-2436) | €42.90 | €42.90 | botnroll (https://www.botnroll.com/en/controller-boards/53-arduino-mega-2560-8058333490083.html) | €42.90 | €42.90
Arduino Mega Proto Shield Rev3 (PCB) | A000080 | 1 | arduino (https://store.arduino.cc/en-pt/products/arduino-mega-proto-shield-rev3-pcb) | (required) | arduino (https://store.arduino.cc/en-pt/products/arduino-mega-proto-shield-rev3-pcb) | €6.35 | €6.35 | robertmauser (https://mauser.pt/catalog/product_info.php?products_id=096-2472) | €6.40 | €6.40 | opencircuit (https://opencircuit.shop/product/arduino-mega-proto-shield-rev3-pcb) | €5.90 | €5.90
Female header stackable 8 pin (10 un.) | - | 1 | opencircuit (https://opencircuit.pt/product/female-header-stackable-8-pin) | (optional) allows to stack protoboard circuits on top of Arduino Mega and/or helps to have easy accessability to PWM and encoders signals using an oscilloscope | opencircuit (https://opencircuit.pt/product/female-header-stackable-8-pin) | €3.05 | €3.05 | - | - | - | - | - | -
Female header stackable 10 pin (10 un.) | - | 1 | opencircuit (https://opencircuit.pt/product/female-header-stackable-10-pin) |  | opencircuit (https://opencircuit.pt/product/female-header-stackable-10-pin) | €3.50 | €3.50 | - | - | - | - | - | -
Female header stackable 2x18 pin (2 un.) | - | 1 | opencircuit (https://opencircuit.pt/product/female-header-stackable-2x18-pin) |  | opencircuit (https://opencircuit.pt/product/female-header-stackable-2x18-pin) | €3.20 | €3.20 | - | - | - | - | - | -
IDC Header Straight 6-Way | - | 8 | - | (optional) although we used IDC connectors to make it compatible with the original cables, you may use other | robertmauser (https://mauser.pt/catalog/product_info.php?products_id=011-0800) | €0.45 | €3.60 | rs (https://pt.rs-online.com/web/p/conectores-macho-para-pcb/8323496) | €0.66 | €5.28 | ptrobotics (https://www.ptrobotics.com/idc/4469-idc-header-straight-6way.html) | €0.25 | €2.00
IDC Socket 6-Way | - | 8 | - |  | robertmauser (https://mauser.pt/catalog/product_info.php?products_id=011-0827) | €0.53 | €4.24 | rs (https://pt.rs-online.com/web/p/conectores-idc/8323648) | €1.09 | €8.72 | ptrobotics (https://www.ptrobotics.com/idc/957-idc-socket-6way.html) | €0.49 | €3.92
Single Board Computer (SBC)
LattePanda 3 Delta | DFR0981 | 1 | lattepanda (https://www.lattepanda.com/lattepanda-3-delta) | - | farnell (https://pt.farnell.com/dfrobot/dfr0981/lattepanda-3-delta-board-2ghz/dp/3954473) | €220.62 | €220.62 | digikey (https://www.digikey.pt/pt/products/detail/dfrobot/DFR0981/16529559) | €265.66 | €265.66 | mouser (https://pt.mouser.com/ProductDetail/DFRobot/DFR0981?qs=t7xnP681wgU%252BVUXJvHqRSQ%3D%3D) | €265.05 | €265.05
Samsung 970 EVO Plus 250 GB PCIe NVMe M.2 | MZ-V7S250BW | 1 | samsung (https://www.samsung.com/pt/memory-storage/nvme-ssd/970-evoplus-nvme-m2-ssd-mz-v7s250bw/) | (optional) if you want to upgrade the 64GB storage (faster read and writing speeds, 64BG for data e.g.) | amazon-es (https://www.amazon.es/dp/B07MHXYL6T) | €48.21 | €48.21 | kuantokusta (https://www.kuantokusta.pt/p/240736/samsung-250gb-970-evo-plus-nvme-m2-mz-v7s250bw) | €51.54 | €51.54 | - | - | -
UGREEN USB 3.0 Hub with 4-Port | CM219 50985 | 1 | ugreen (https://eu.ugreen.com/products/ugreen-usb-hub-3-0-ultra-slim-4-port-usb-3-hub-with-5gbps-data-transfer) | (optional) increases #USB ports available (e.g., joystick, keyboard and/or mouse adapter, etc.) | amazon-es (https://www.amazon.es/-/pt/dp/B0CD1BHXPZ) | €12.19 | €12.19 | kuantokusta (https://www.kuantokusta.pt/p/10379518/ugreen-hub-usb-4-portas-usb-30-cinza) | - | - | - | - | -
Single Board Computer (SBC) Battery (optional: power SBC through USB C PD protocol; if not used, DC/DC buck-boost converter to have 11-15VDC)
Powerbank Xiaomi Mi 50W 20000 mAh | PB200SZM | 1 | xiaomi (https://www.mi.com/global/product/mi-50w-power-bank-20000/) | (preferred) 50W > minimum 24W, if 3A current consumption the 20000mAh allows for 6h+ | amazon-es (https://www.amazon.es/-/pt/dp/B0BFBBQQXK) | €80.17 | €80.17 | kuantokusta (https://www.kuantokusta.pt/p/7781139/xiaomi-mi-50w-20000-mah-black) | €50.46 | €50.46 | - | - | -
UGREEN Nexode Powerbank 100W 20000mAh | - | 1 | ugreen (https://eu.ugreen.com/products/25188) | (not tested!) | amazon-es (https://www.amazon.es/-/pt/dp/B0C3GTMX5M) | €81.32 | €81.32 | ugreen (https://eu.ugreen.com/products/25188) | €69.99 | €69.99 | - | - | -
Networking (optional: default network interfaces of the SBC may be ok for you)
Bingfu Antena WiFi Dual Band RP-SMA 25cm U.FL IPX IPEX MHF4 M.2 NGFF Intel | BFN00525 | 1 | bingfu (https://bingfushop.com/products/bingfu-u-fl-ipx-ipex-mhf4-to-rp-sma-female-bulkhead-mount-wifi-antenna-cable-30cm-12-inch-2-pack-for-intel-ax200ngw-8265ac-826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) | (optional) same Wi-Fi antennas as in F1TENTH | amazon-es (https://www.amazon.es/dp/B08FX3QXRQ) | €12.19 | €12.19 | - | - | - | - | - | -
Brainboxes 5 Port Unmanaged Ethernet Switch 10/100Mbps | SW-005 | 1 | brainboxes (https://www.brainboxes.com/files/catalog/product/SW/SW-005/documents/SW-005-datasheet.pdf) | (optional) if you want to have multiple 2D/3D LiDARs communicating to the SBC (single ethernet port…) | farnell (https://pt.farnell.com/brainboxes/sw-005/switch-n-w-5port-100mbps-din-rail/dp/2383213) | €61.30 | €61.30 | digikey (https://www.digikey.pt/pt/products/detail/brainboxes/SW-005/10707220) | €48.41 | €48.41 | mouser (https://pt.mouser.com/ProductDetail/Brainboxes/SW-005?qs=BJlw7L4Cy7944%2FIWYfp8eA%3D%3D) | €48.30 | €48.30
Brainboxes 5 Port Unmanaged Ethernet Switch 10/100/1000Mbs | SW-015 | 1 | brainboxes (https://www.brainboxes.com/files/catalog/product/SW/SW-015/documents/SW-015-datasheet.pdf) | (optional) some 3D LiDAR may surpass the 100Mbps requirement (depending on the configuration) | farnell (https://pt.farnell.com/brainboxes/sw-015/ernet-switch-unmanaged-gigabit/dp/3604249) | €102.29 | €102.29 | digikey (https://www.digikey.pt/pt/products/detail/brainboxes/SW-015/13152346) | €95.04 | €95.04 | mouser (https://pt.mouser.com/ProductDetail/Brainboxes/SW-015?qs=W%2FMpXkg%252BdQ6e4NboBK2WDQ%3D%3D) | €87.12 | €87.12
UGREEN RJ45 female coupler Gigabit Ethernet 1000Mbps | NW114 20390 | 1 | ugreen (https://www.ugreen.pl/en/products/cables/ethernet/ugreen-network-connector-ethernet-rj45-10-gbps-network-cable-connector-black-nw114-20390-99748) | (optional) facilitates the connection of the Hokuyo UST-10LX (short Ethernet cable) | amazon-es (https://www.amazon.es/-/pt/dp/B016B13U5S) | €3.66 | €3.66 | kuantokusta (https://www.kuantokusta.pt/p/7909830/ugreen-extensao-nw114-uniao-rj45-preta?sort=5) | €3.90 | €3.90 | - | - | -
Miscellaneous
XT30 Connector - Pair Male/Female | xt30 | 10 | - | (optional) DC derivation bus to power the sensors | botnroll | €1.50 | €15.00 | digikey (https://www.digikey.pt/pt/products/detail/dfrobot/FIT0586/9559255) | €1.81 | €18.10 | aliexpress (https://www.aliexpress.us/item/3256806414638022.html) | €0.26 | €2.60
XT60 Connector - Pair Male/Female | xt60 | 5 | - | (optional) connection from the inside to the exterior of the original Discovery Q2 metallic box | botnroll (https://www.botnroll.com/en/xt-t-deans/219-prt-10474-conector-xt60-macho-e-femea.html) | €1.50 | €7.50 | digikey (https://www.digikey.pt/pt/products/detail/dfrobot/FIT0587/9559256) | €1.43 | €7.15 | aliexpress (https://www.aliexpress.us/item/3256806917123984.html) | €0.21 | €1.05
Terminal Blocks 10mm² VDE DIN EN 60998 - DIN EN 60999 | 096-9065 | 2 | robertmauser (https://mauser.pt/catalog/product_info.php?products_id=096-9065) | GND and Vcc (Vbattery or Vbms) buses | robertmauser (https://mauser.pt/catalog/product_info.php?products_id=096-9065) | €2.17 | €4.34 | - | - | - | - | - | -
Sensors (depends on your desired perception system! Here only put the ones tested with the modified platform)
Inertial Measurement Units (IMUs)
Xsens MTi-3 AHRS | MTi-3-5A-DK | 1 | xsens (https://www.movella.com/products/sensor-modules/xsens-mti-3-ahrs) | - | mouser (https://pt.mouser.com/ProductDetail/Movella-Xsens/MTi-3-5A-DK?qs=9vOqFld9vZVm8SUT4T13Og%3D%3D) | €458.85 | €458.85 | digikey (https://www.digikey.pt/pt/products/detail/xsens-a-movella-brand/MTI-3-5A-DK/18718047) | €427.54 | €427.54 | farnell (https://pt.farnell.com/xsens/mti-3-0i-dk/dev-kit-3-axis-accel-gyro-magnetometer/dp/3793984) | €419.99 | €419.99
Xsens MTi-630 AHRS | MTi-630-DK | 1 | xsens (https://www.movella.com/products/sensor-modules/xsens-mti-630-ahrs) | - | mouser (https://pt.mouser.com/ProductDetail/Movella-Xsens/MTi-630-DK?qs=T3oQrply3y%2Fij%2F%252BbZ6p1ew%3D%3D) | €1054.50 | €1054.50 | digikey (https://www.digikey.pt/pt/products/detail/xsens-a-movella-brand/MTI-630-DK/10294560) | €1086.38 | €1086.38 | farnell (https://pt.farnell.com/xsens/mti-630-dk/development-kit-inertial-sensor/dp/3225728) | €1034.00 | €1034.00
2D Laser Scanners
Hokuyo UST-10LX-H01/H02 | UST-10LX | 1 | hokuyo-usa (https://hokuyo-usa.com/products/lidar-obstacle-detection/ust-10lx) | - | robotshop (https://eu.robotshop.com/products/hokuyo-ust-10lx-scanning-laser-rangefinder-eu) | €1783.50 | €1783.50 | generationrobots (https://www.generationrobots.com/en/401755-hokuyo-ust-10lx-scanning-laser-range-finder.html) | €1878.00 | €1878.00 | - | - | -
LDRobot D300 Kit LD-19 | D300 | 1 | ldrobot (https://www.ldrobot.com/ProductDetails?sensor_name=D300+Kit) | - | robotshop (https://eu.robotshop.com/products/ldrobot-d300-lidar-kit) | €121.77 | €121.77 | amazon-es (https://www.amazon.es/-/pt/dp/B0B1VD2PJH) | €60.98 | €60.98 | dfrobot (https://www.dfrobot.com/product-2610.html) | $119.00 | $119.00
SLAMTEC RPLIDAR S2 | S2 | 1 | slamtec (https://www.slamtec.com/en/S2) | - | robotshop (https://eu.robotshop.com/products/rplidar-s2-360-laser-scanner-30-m) | €471.88 | €471.88 | generationrobots (https://www.generationrobots.com/en/403961-360-degree-laser-scanner-rplidar-s2.html) | €536.64 | €536.64 | amazon-es (https://www.amazon.es/-/pt/dp/B0B1MJSWCD) | €405.59 | €405.59
YDLIDAR X4 | X4 | 1 | ydlidar (https://www.ydlidar.com/products/view/5.html) | - | xiaor-geek (https://www.xiaorgeek.net/products/ydlidar-x4-lidar-ranging-sensor-module) | $96.99 | $96.99 | rlx (https://rlx.sk/en/object-detection-proximity-sensor-lidar-gesture/6388-ydlidar-x4-360-degree-2d-lidar-ranging-sensor-for-ros-robot-slam-3d-reconstruction-er-s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) | €128.17 | €128.17 | - | - | -
3D Light Detection And Ranging (LiDAR)
Livox Mid-360 | mid-360 | 1 | livox (https://www.livoxtech.com/mid-360) | - | livox (https://store.dji.com/pt/product/livox-mid-360) | €659.00 | €659.00 | - | - | - | - | - | -
Ouster OS1 64 | os1-64 | 1 | ouster (https://ouster.com/products/hardware/os1-lidar-sensor) | - | - | - | - | - | - | - | - | - | -
RoboSense RS-HELIOS-5515 | rs-helios-5515 | 1 | robosense (https://www.robosense.ai/en/rslidar/RS-Helios) | - | robotshop (https://eu.robotshop.com/products/robosense-rs-helios-5515-lidar-150-m) | €5166.00 | €5166.00 | generationrobots (https://www.generationrobots.com/en/403897-rs-helios-32-5515-3d-lidar-laser-range-finder.html) | €4742.40 | €4742.40 | - | - | -
Velodyne VLP-16 | vlp-16 | 1 | ouster (https://ouster.com/products/hardware/vlp-16) | - | - | - | - | - | - | - | - | - | -
RGB + Depth Cameras
Intel RealSense D455 | d455 | 1 | intel (https://www.intelrealsense.com/depth-camera-d455/) | - | mouser (https://pt.mouser.com/ProductDetail/Intel/82635DSD455?qs=sPbYRqrBIVkW8YqcWqMK9g%3D%3D) | €439.66 | €439.66 | digikey (https://www.digikey.pt/pt/products/detail/intel-realsense/82635DSD455/12429610) | €423.73 | €423.73 | rs (https://pt.rs-online.com/web/p/camaras-de-profundidad/2026353) | €676.78 | €676.78
Intel RealSense L515 | l515 | 1 | intel (https://www.intelrealsense.com/lidar-camera-l515/) | - | digikey (https://www.digikey.pt/pt/products/detail/intel-realsense/82638L515G1PRQ/11688015) | €595.13 | €595.13 | - | - | - | - | - | -
OAK-D Pro Fixed Focus | A00565 | 1 | luxonis (https://shop.luxonis.com/products/oak-d-pro) | - | luxonis (https://shop.luxonis.com/products/oak-d-pro) | $349.00 | $349.00 | mouser (https://pt.mouser.com/ProductDetail/Luxonis/OAK-D-PRO-FF?qs=Znm5pLBrcAK58KqDdxCLeQ%3D%3D) | €331.55 | €331.55 | digikey (https://www.digikey.pt/pt/products/detail/arducam/OAK-D-PRO-FF/23570902) | €490.82 | €490.82

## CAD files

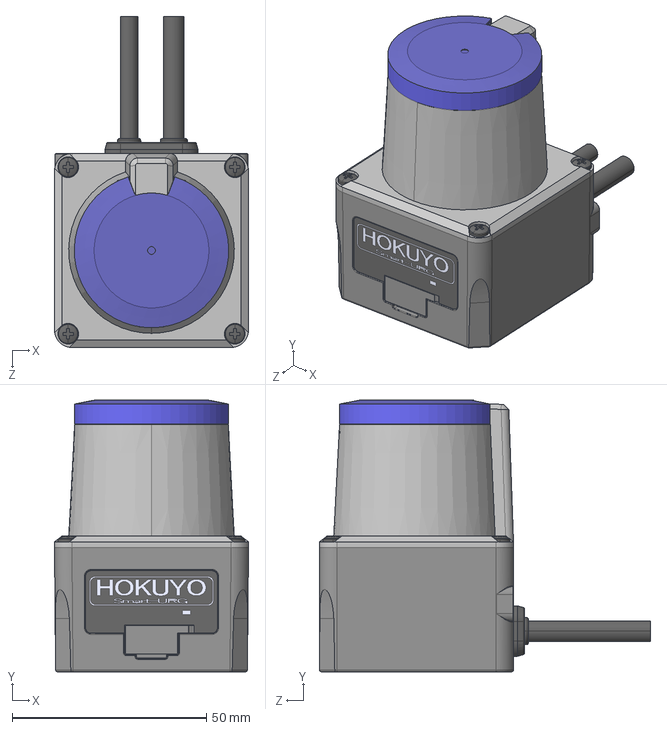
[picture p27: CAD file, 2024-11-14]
docs/assets/sensors/lidar2d/hokuyo_ust-10lx/hokuyo_ust-10lx_3d-model.STEP
50.0 x 70.0 x 85.3 mm

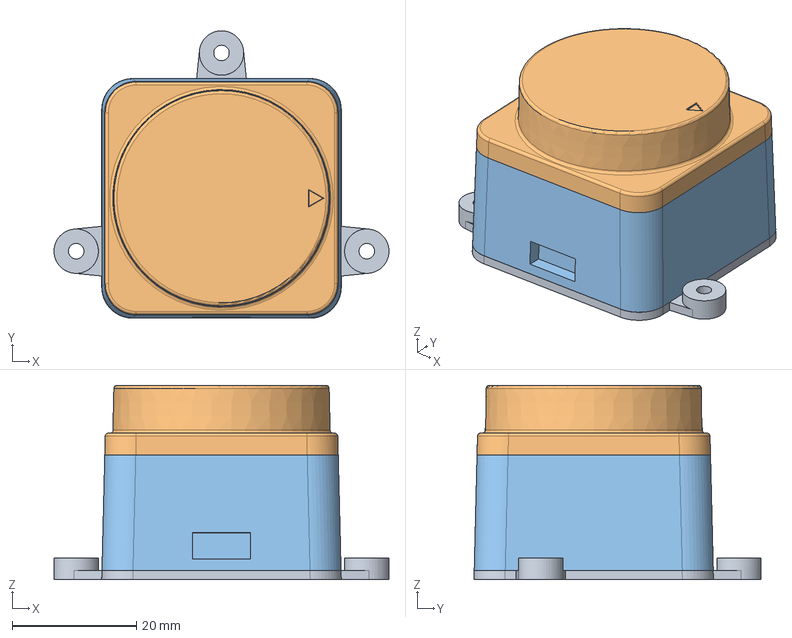
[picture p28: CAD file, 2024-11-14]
docs/assets/sensors/lidar2d/ldrobot_d300_ld19/ldrobot_d300_ld19_3d-model.step
54.0 x 46.3 x 31.3 mm
LD19_BASE
LD19_EMITTER
LD19_BODY

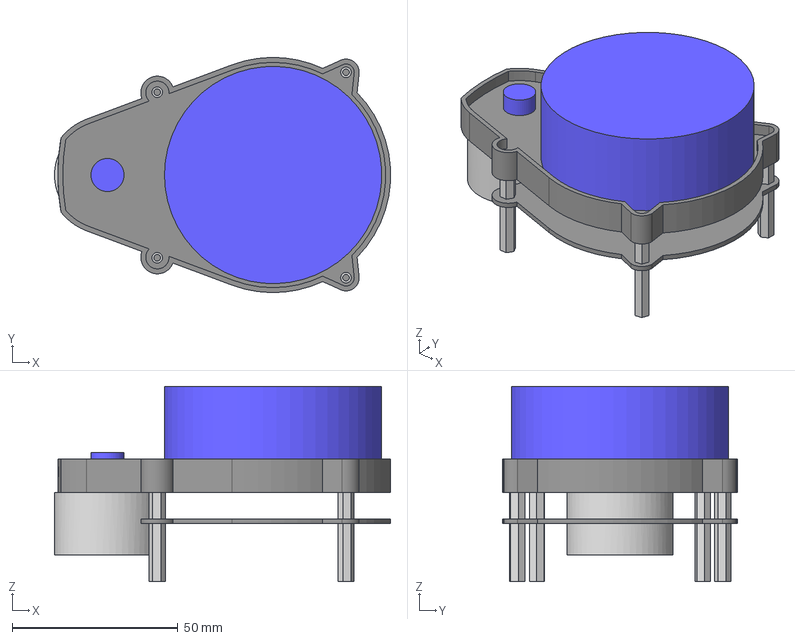
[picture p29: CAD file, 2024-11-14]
docs/assets/sensors/lidar2d/ydlidar_x4/ydlidar_x4_3d-model.step
101.4 x 71.0 x 59.0 mm

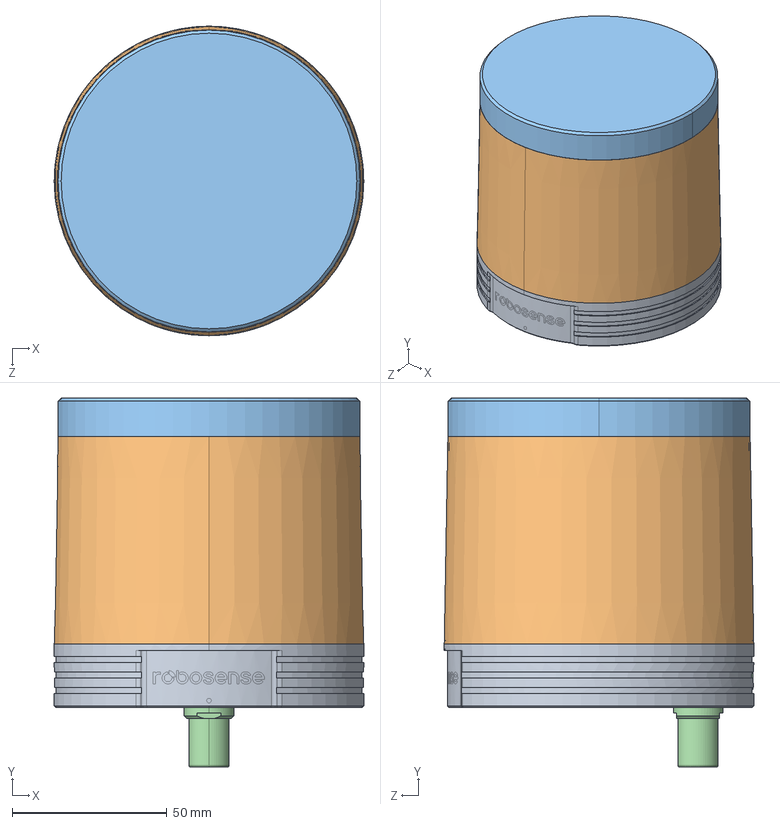
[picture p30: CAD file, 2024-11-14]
docs/assets/sensors/lidar3d/robosense_rs-helios_5515/robosense_rs-helios-5515_3d-model.STEP
100.0 x 119.2 x 100.0 mm
20202-0182-04 菁釱
20402-0022-01 悵誘欶
20202-0225-04 階裔
20107-0059-00 瑤脣芛
20208-0025-00 芵ァ概

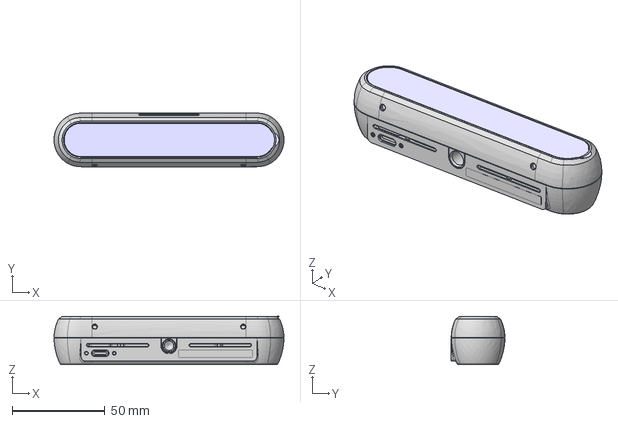
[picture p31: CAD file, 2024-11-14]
docs/assets/sensors/rgbd/intel_realsense_d455/intel_realsense_d455_3d-model.step
123.9 x 29.1 x 26.0 mm

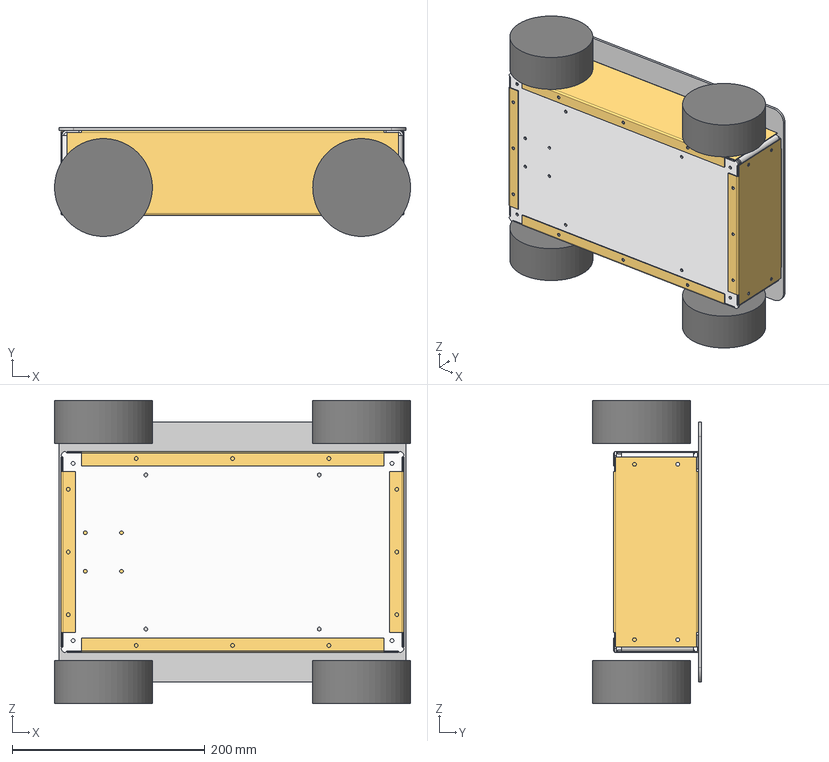
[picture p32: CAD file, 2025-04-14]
models/v1/hangfa-discovery-q2_mechanical-platform.step
369.5 x 113.0 x 315.0 mm
Base Plate v1
Side Plate
Front Back Plate x 2
Plate Joint x 2
Side Plate Inv
Plate Joint Inv x 2
Base Suspension
Wheels Suspension
Top Plate
Wheel Body x 4

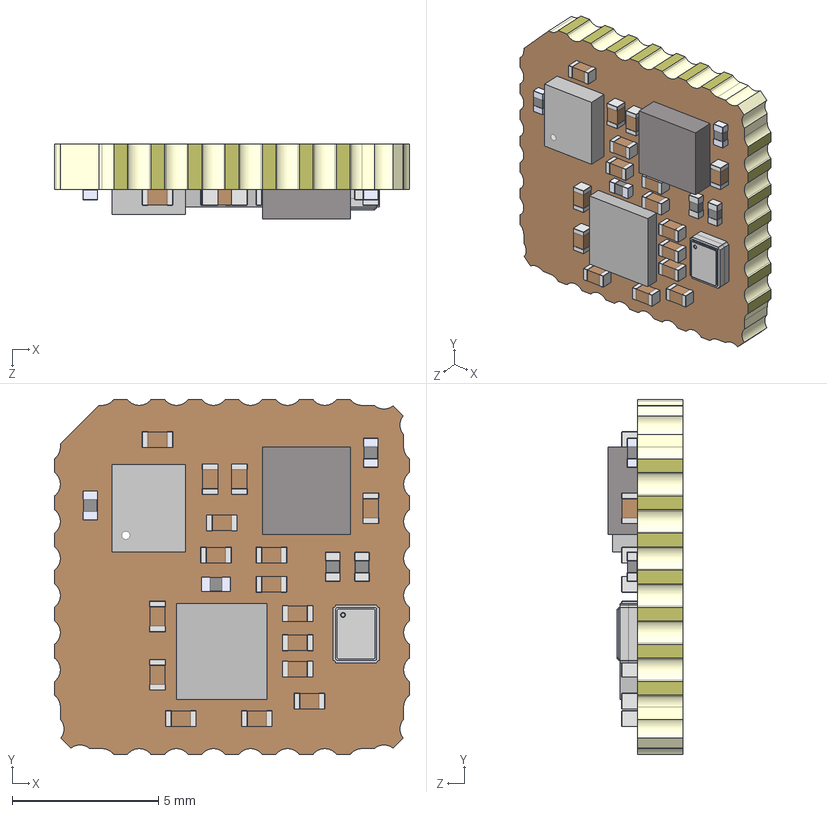
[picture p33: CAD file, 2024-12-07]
docs/assets/sensors/imu/xsens_mti-3-ahrs/xsens_mti-3-ahrs_3d-model_mti-1-series_v3.STEP
12.1 x 12.1 x 2.56 mm
Extruded(2)^7460079024(2)_U200_1v2(2)_MTi-1-SoB_v2
Cap_0402(2)^C200_1v2(2)_MTi-1-SoB_v2
Cap_0402(2)^C201_1v2(2)_MTi-1-SoB_v2
Cap_0402(2)^C204_1v2(2)_MTi-1-SoB_v2
Cap_0402(2)^C205_1v2(2)_MTi-1-SoB_v2
Cap_0402(2)^C206_1v2(2)_MTi-1-SoB_v2
Cap_0402(2)^C207_1v2(2)_MTi-1-SoB_v2
Cap_0402(2)^C208_1v2(2)_MTi-1-SoB_v2
Cap_0402(2)^C209_1v2(2)_MTi-1-SoB_v2
Cap_0402(2)^C300_1v2(2)_MTi-1-SoB_v2
Cap_0402(2)^C301_1v2(2)_MTi-1-SoB_v2
Cap_0402(2)^C302_1v2(2)_MTi-1-SoB_v2
Cap_0402(2)^C303_1v2(2)_MTi-1-SoB_v2
Cap_0402(2)^C305_1v2(2)_MTi-1-SoB_v2
Cap_0402(2)^C304_1v2(2)_MTi-1-SoB_v2
RES0402(2)^R200_1v2(2)_MTi-1-SoB_v2
RES0402(2)^R300_1v2(2)_MTi-1-SoB_v2
RES0402(2)^R301_1v2(2)_MTi-1-SoB_v2
Extruded-1(2)^6752205952(2)_S300_1v2(2)_MTi-1-SoB_v2
User_Library-LGA-14_2_5x3(2)^S301_1v2(2)_MTi-1-SoB_v2
RES0402(2)^R302_1v2(2)_MTi-1-SoB_v2
Cap_0402(2)^C202_1v2(2)_MTi-1-SoB_v2
Cap_0402(2)^C203_1v2(2)_MTi-1-SoB_v2
User_Library-Crystal_(NDK)_2.0x1.6(2)^Y200_1v2(2)_MTi-1-SoB_v2
RES0402(2)^R303_1v2(2)_MTi-1-SoB_v2

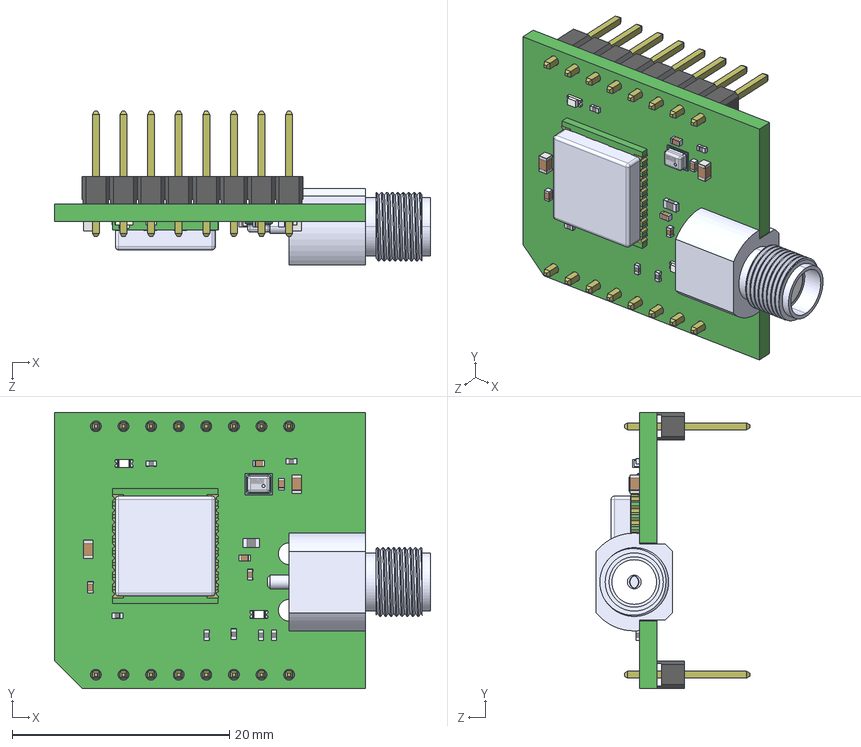
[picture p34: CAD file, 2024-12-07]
docs/assets/sensors/imu/xsens_mti-3-ahrs/xsens_mti-3-ahrs_3d-model_mti-1-series_v2_dk-gnss.STEP
34.6 x 25.4 x 14.1 mm
RES0402 x 7
MAX-8
Cap_0402 x 4
SW3dPS-LED SMD0603 x 2
SW3dPS-LED SMD0603-4 x 2
SW3dPS-LED SMD0603-1 x 2
SW3dPS-LED SMD0603-3 x 2
SW3dPS-LED SMD0603-2 x 2
RES0603
Cap_0603 x 2
User Library-BST-BMP280
User Library-cap_0402
BoardGNSS_
2pin, 2.54mm, DIP, single row x 8
SMA-J-P-H-ST-EM3

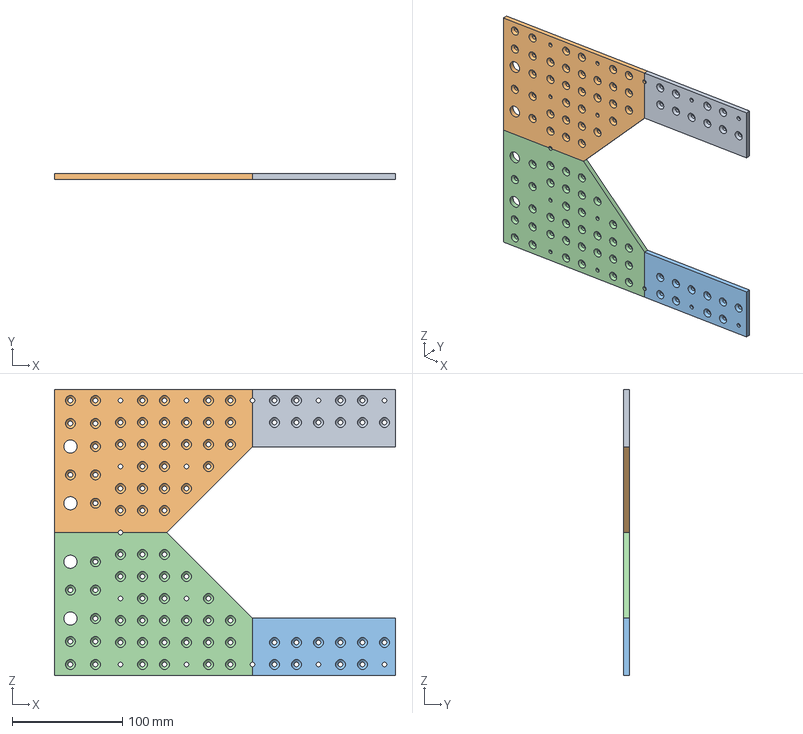
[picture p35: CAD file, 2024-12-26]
models/v1/hangfa-discovery-q2_optitrack_sensors-plate_trackers-support.step
310.0 x 5.00 x 260.0 mm
hangfa-discovery-q2_optitrack_sensors-plate_trackers-support_front-ri ght
hangfa-discovery-q2_optitrack_sensors-plate_trackers-support_back-rig ht
hangfa-discovery-q2_optitrack_sensors-plate_trackers-support_front-le ft
hangfa-discovery-q2_optitrack_sensors-plate_trackers-support_back-lef t

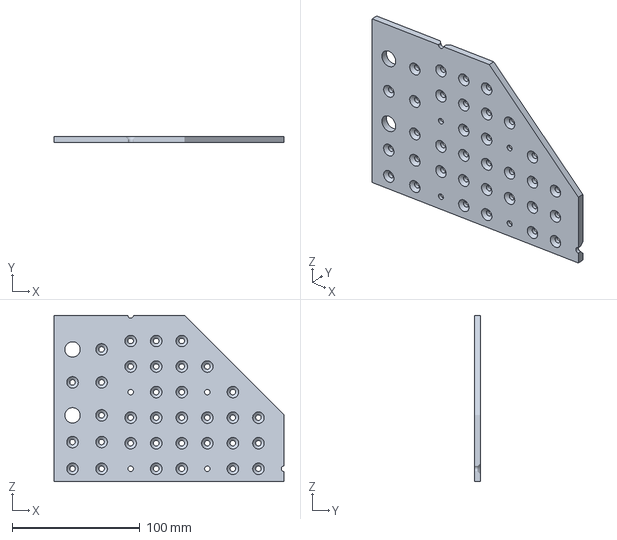
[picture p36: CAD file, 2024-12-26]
models/v1/hangfa-discovery-q2_optitrack_sensors-plate_trackers-support_back-left.3mf
180.0 x 5.00 x 130.0 mm

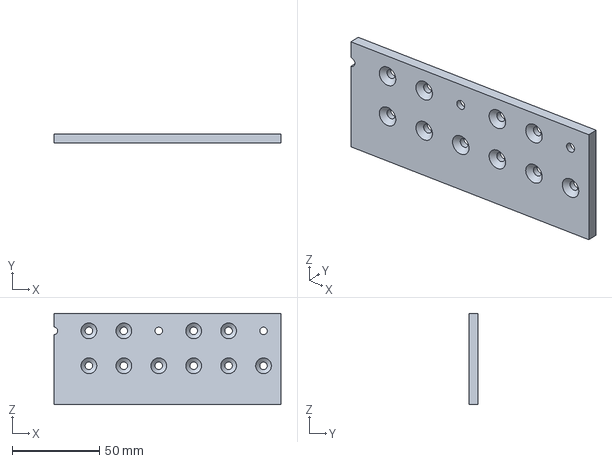
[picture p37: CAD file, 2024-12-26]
models/v1/hangfa-discovery-q2_optitrack_sensors-plate_trackers-support_front-right.3mf
130.0 x 5.00 x 52.2 mm

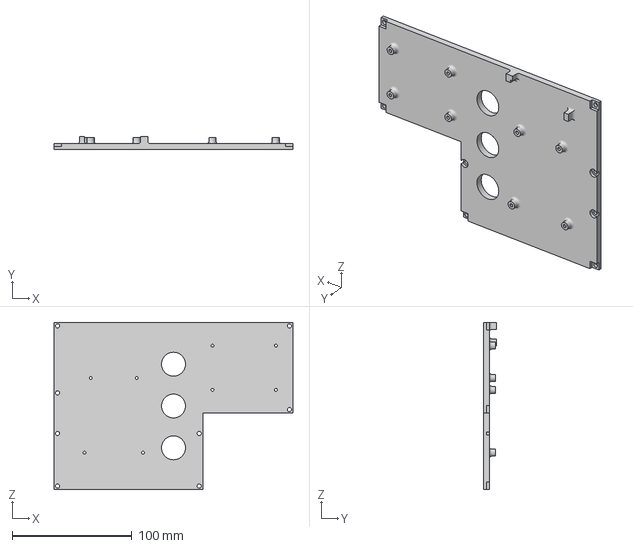
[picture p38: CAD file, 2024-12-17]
models/v1/electronics_baseplate_level.3mf
200.0 x 11.0 x 140.0 mm

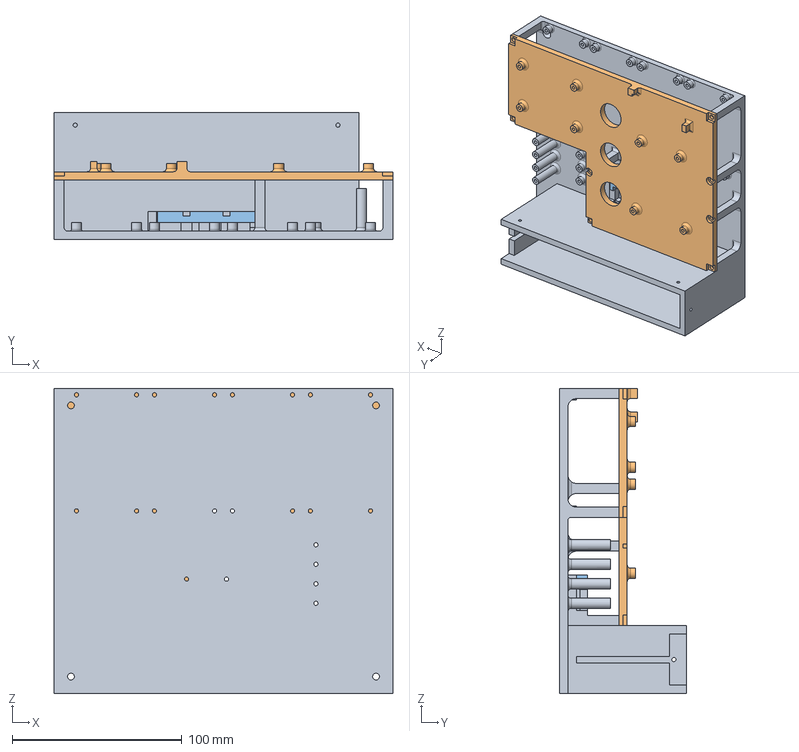
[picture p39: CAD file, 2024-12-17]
models/v1/electronics_baseplate.step
200.0 x 75.0 x 180.0 mm

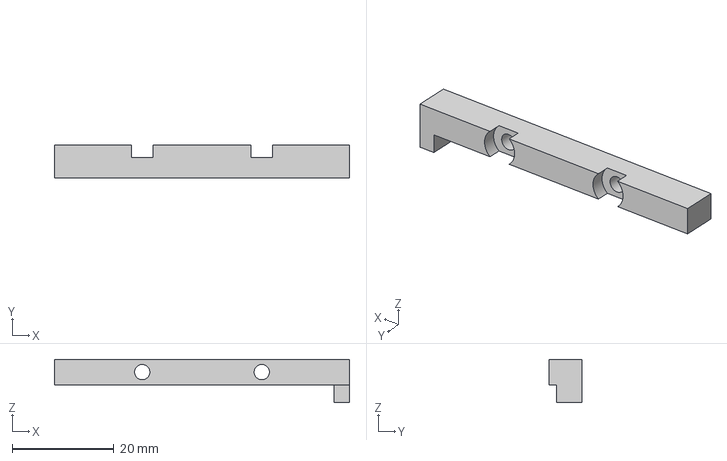
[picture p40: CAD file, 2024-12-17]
models/v1/electronics_baseplate_bms-fixation.3mf
58.0 x 6.50 x 8.50 mm

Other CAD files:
models/v1/sensors-plate_imu_xsens-mti-3-ahrs_support.step
models/v1/hangfa-discovery-q2_optitrack_sensors-plate_trackers-support_back-right.3mf
models/v1/hangfa-discovery-q2_optitrack_sensors-plate_trackers-support_front-left.3mf
models/v1/electronics_baseplate_base.3mf
docs/assets/sensors/imu/xsens_mti-3-ahrs/xsens_mti-3-ahrs_3d-model_mti-1-series_v2.STEP
models/v0/battery_xiaomi-powerbank-20000mAh_box.f3d
models/v0/electronics_baseplate.f3d
models/v0/platform_hangfa-discovery-q2_draft.f3d
models/v0/platform_hangfa-discovery-q2_stand-up-support.f3d
models/v0/platform_hangfa-discovery-q2_top-plate-support-basic.f3d
models/v0/sensors_lidar2d_hokuyo_ust-10lx.f3d
models/v0/sensors_lidar2d_hokuyo_ust-10lx_support.f3d
models/v0/sensors_lidar3d_robosense_rs-helios-5515.f3d
models/v0/sensors_lidar3d_robosense_rs-helios-5515_support.f3d
models/v0/sensors_rgbd_intel_realsense_d455.f3d
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

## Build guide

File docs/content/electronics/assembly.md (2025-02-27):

# Assembly

## 3D Electronics Framework

**3D Model**

- [AutoDesk Fusion 360](https://github.com/sousarbarb/inesctec_mrdt_hangfa_discovery_q2/blob/main/models/v1/electronics_baseplate.f3d)
- [STEP](https://github.com/sousarbarb/inesctec_mrdt_hangfa_discovery_q2/blob/main/models/v1/electronics_baseplate.step)

**Legend**

- **A:** Tattu 10000mAh 11.1V 15C 3S LiPo Battery
- **B:** 18650 BMS Charger 3S 12.6V 20A Rev. 2.0
- **C:** voltage and ground electric buses
- **D:** Faulhaber 2342 OEM DC Motors (and optical encoders with 12 CPR)
- **E:** Cytron 13A 5-30V Single DC Motor Driver
- **F:** Arduino Mega 2560 Rev3 + Arduino Mega Proto Shield Rev3 (PCB)
- **G:** DC 5-30V to 1.25-30V 8A Buck Boost Converter

### Base Plate

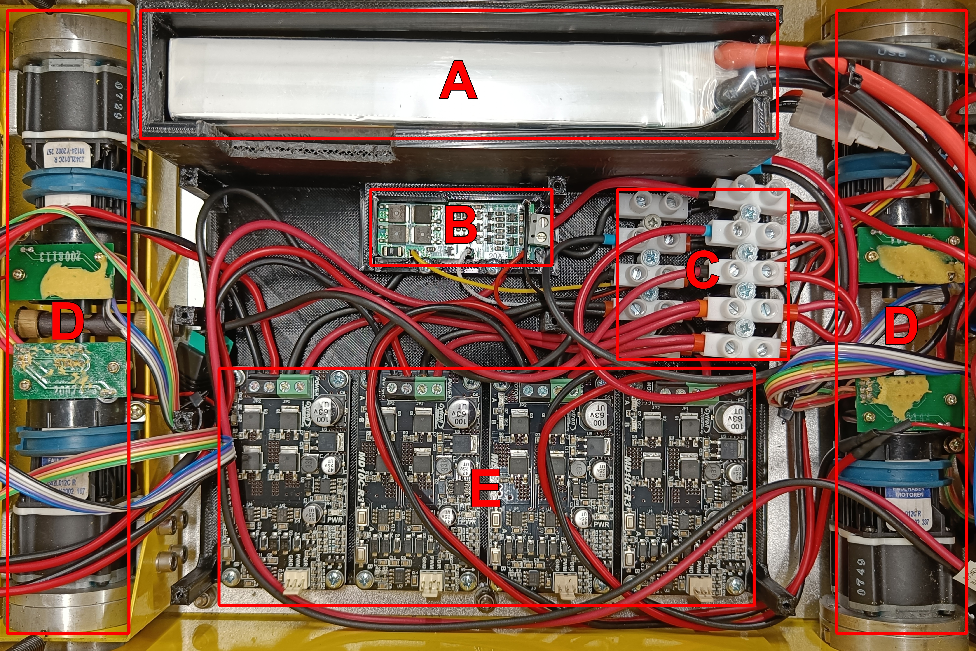
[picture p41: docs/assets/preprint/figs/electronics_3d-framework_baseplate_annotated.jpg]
Baseplate


### First Level

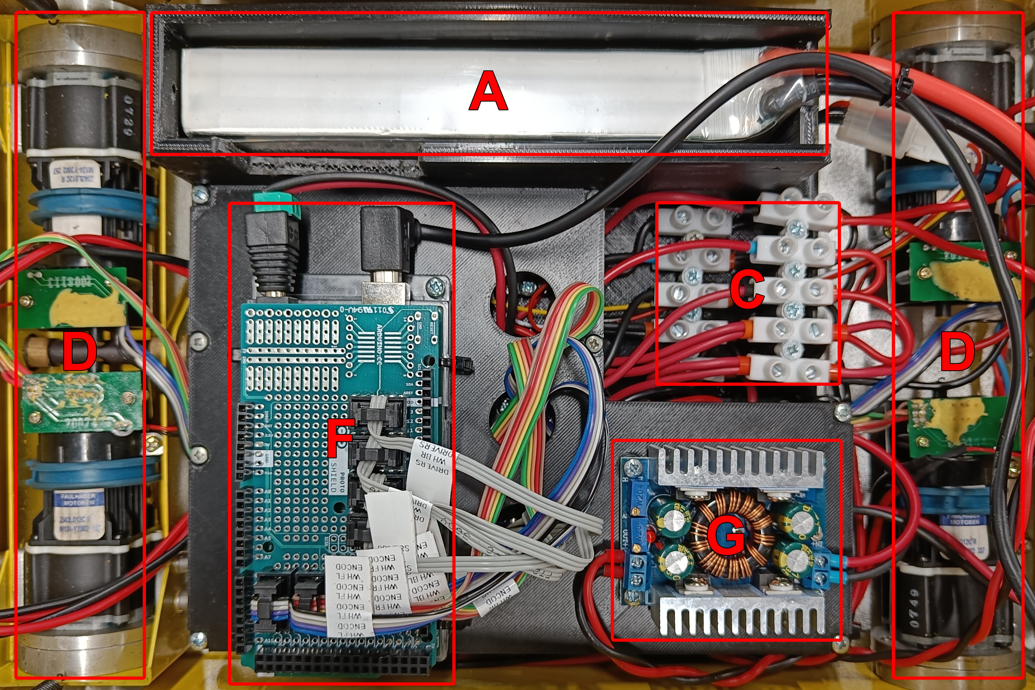
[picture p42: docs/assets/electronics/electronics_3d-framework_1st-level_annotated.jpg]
1st Level


## Arduino Mega Proto Shield

**Documents**

- [Arduino Mega 2560 - Proto Shield Connections](../../assets/electronics/arduino-mega-2560_proto-shield_connections.pdf)
- [Hangfa Discovery Q2 - Encoders Pinout](../../assets/electronics/hangfa-discovery-q2_encoders_pinout.pdf)

**Legend**

- **A:** motor drivers connectors (GND, PWM, direction)
- **B:** encoders connectors (GND, CHA, CHB, Vcc) with 3.3kΩ pull-up resistors
- **C:** Arduino Mega standard headers

### Front View

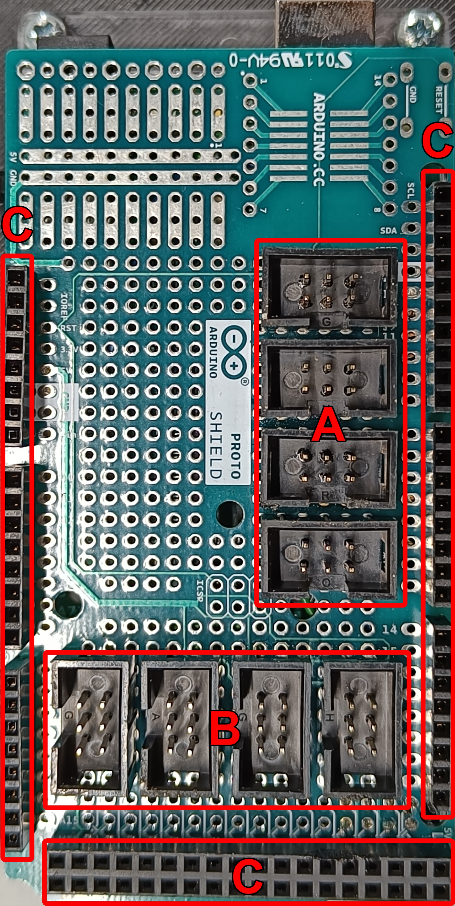
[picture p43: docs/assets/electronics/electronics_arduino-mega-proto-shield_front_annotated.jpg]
Arduino Mega Proto Shield - Front View


### Back View

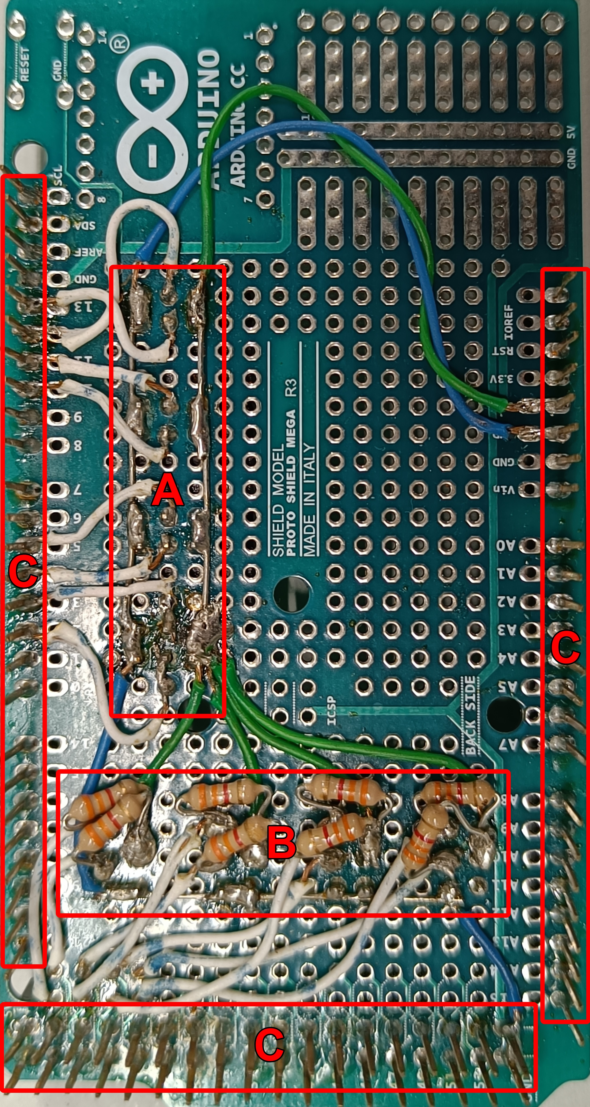
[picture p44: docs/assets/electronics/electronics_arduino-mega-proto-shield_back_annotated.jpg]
Arduino Mega Proto Shield - Back View


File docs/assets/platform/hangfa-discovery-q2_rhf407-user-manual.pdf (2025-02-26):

## Robot Main Control Board (RHF407) User Manual Ver：1.1

## Catalogue

4.1.2 | Serial port control command | 59
4.2 | Routine introduction | 60
4.2.1 | Routine function | 60
4.2.2 | Set up project | 60
4.2.3 | Key file description | 63

## Figure directory

Figure 1．Development board external view | 4
Figure 2．The processor circuit | 6
Figure 3．The reset circuit | 7
Figure 4．Low frequency crystal circuit | 7
Figure 5．JTAG circuit | 8
Figure 6．The power circuit | 8
Figure 7．Indicator light circuit | 9
Figure 8．The button circuit | 9
Figure 9．RS232 serial port circuit | 9
Figure 10．TTL serial port circuit | 10
Figure 11．RS485 circuit | 10
Figure 12．CAN bus circuit | 11
Figure 13．I2C interface circuit | 12
Figure 14．TF cardcircuit | 12
Figure 15．LCD module interface circuit | 13
Figure 16．ADC circuit | 13
Figure 17．DAC circuit | 14
Figure 18．PWM output circuit | 14
Figure 19．Establish a new MDK project | 16
Figure 20．Select the MDK device | 17
Figure 21．MDK empty project | 17
Figure 22．Add a file | 18
Figure 23．Configure the compiler | 19
Figure 24．Configure the debugger | 20
Figure 25．Configure the downloader | 20
Figure 26．Add the code | 21

## 1 Hardware description

This chapter will detail RHF407 development board of hardware resources, which gives users a detailed understanding of the functions and characteristics of the development board.

## 1.1 Robot main control board (RHF407) introduction

All the source code has compiled under MDK5.0.5 and verification through on the development board.
This development board is based on STM32F407VE processor, which mainly providing users with a demonstration platform.

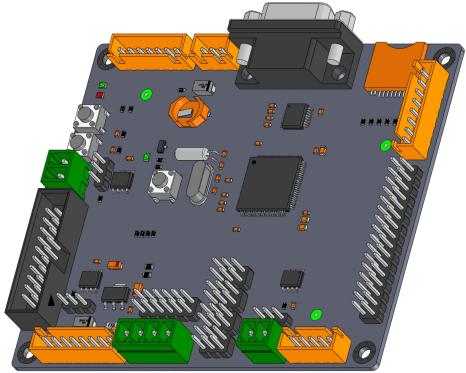
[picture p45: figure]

Figure 1．Development board external view

On-board resources are as follows:
l STM32F407VET6 is based on the high-performance ARM Cortex-M4 32-bit RISC core operating at a frequency of up to 168 MHz. incorporates high-speed embedded memories (Flash memory up to 1 M byte, up to 192 Kbytes of SRAM), up to 4 Kbytes of backup SRAM.
l Two RS232 level UART serial ports. One port can be directly connected to the PC, another can be connected to other equipment via 3 white pin terminal.
l A TTL level UART serial port with three general IO ports, which can be connected to the need to control other devices.
l A RS485 interface
l A reset signal status led
l Two programmed control led
l A reset switch
l Two normally open input keys
l A TF card interface, using the SPI bus
l A TFT LCD interface, you can use the FSMC, with SPI interface, sharing and TF card interface.
l Two CAN bus interfaces
l Two DAC output interfaces
l Eight ADC input interfaces
l Eight PWM output interfaces
l A I2C interface, which can be used as the PWM3 or PWM4 interface l An RTC back-up battery interface
l A JTAG interface(20pin)
PCB size is 86 mm x 100 mm.

## 1.2 Circuit description

## 1.2.1 The processor circuit

Part of the processor circuit is as shown in the figure below.

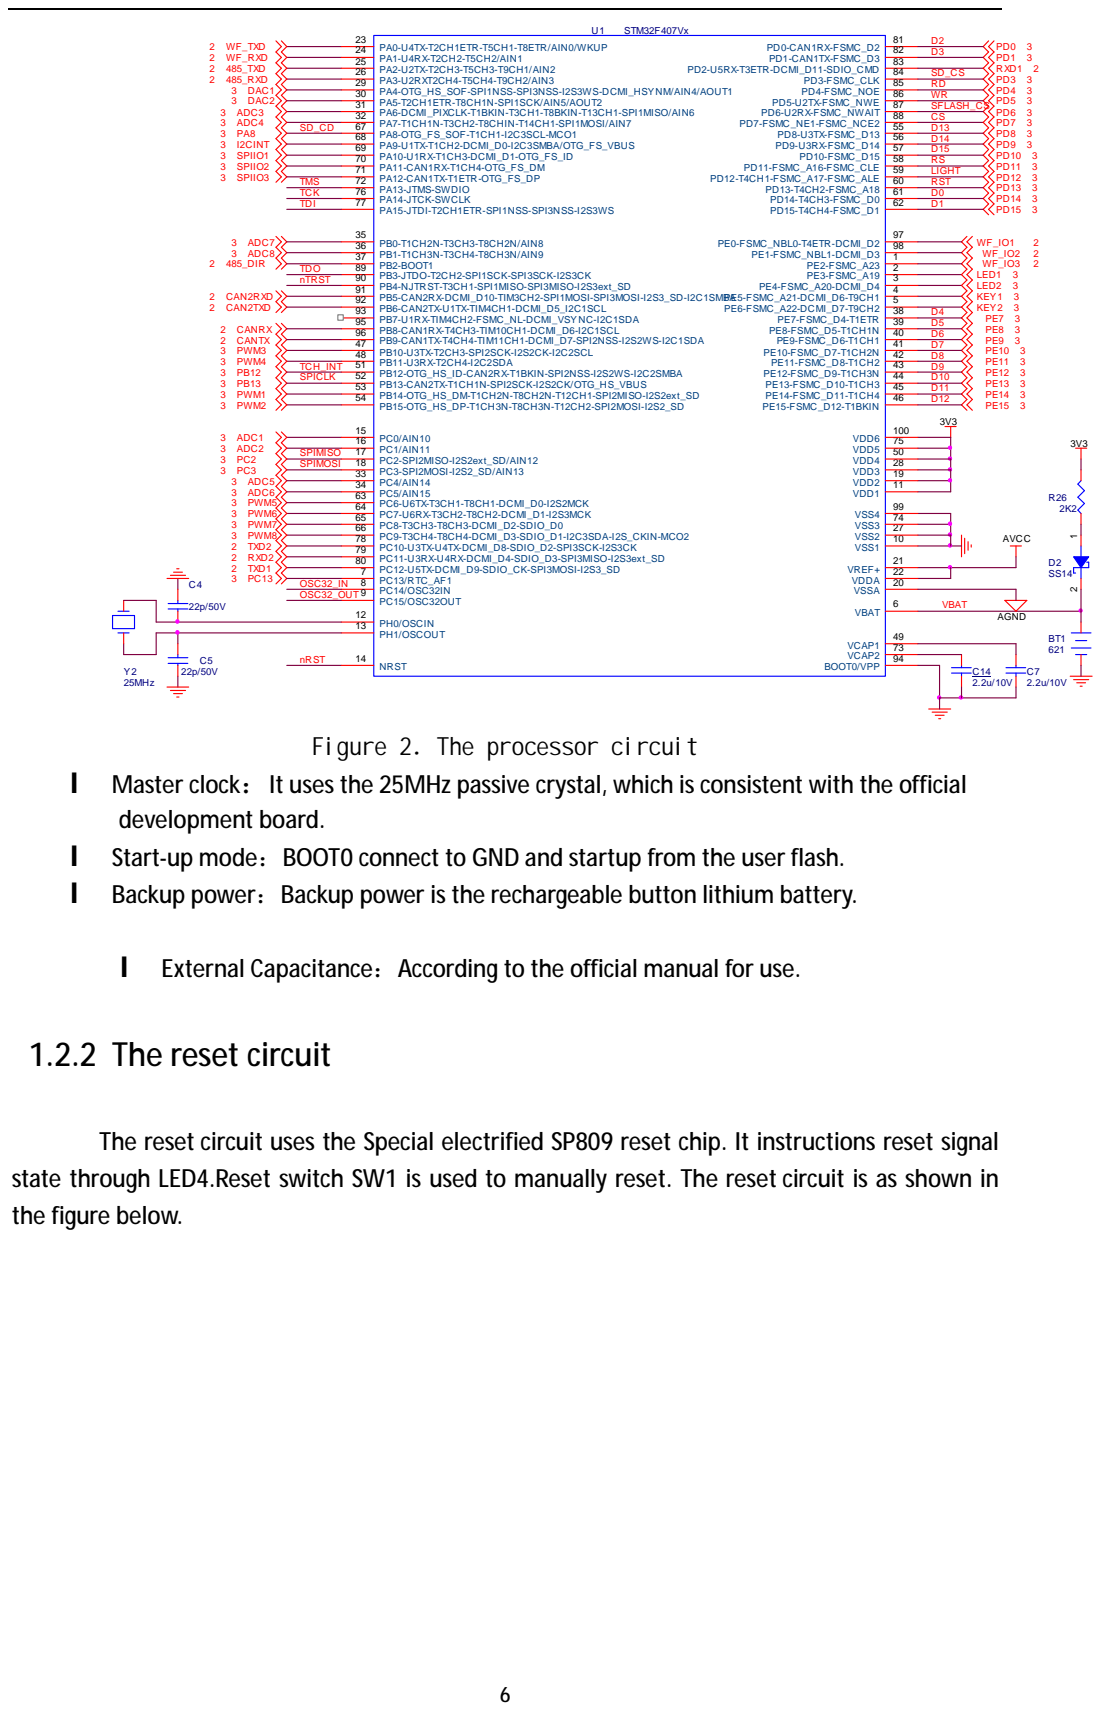
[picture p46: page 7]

Figure 2．The processor circuit

l Master clock：It uses the 25MHz passive crystal, which is consistent with the official
development board.
l Start-up mode：BOOT0 connect to GND and startup from the user flash.
l Backup power：Backup power is the rechargeable button lithium battery.

l External Capacitance：According to the official manual for use.

The reset circuit uses the Special electrified SP809 reset chip. It instructions reset signal
state through LED4.Reset switch SW1 is used to manually reset. The reset circuit is as shown in
the figure below.

Figure 3．The reset circuit

## 1.2.3 Low frequency crystal circuit

Low frequency crystal circuit uses the 32.768MHz passive crystal as shown in the figure below.

Y1
32.768KHz

C2
6.8p/50V

C3
6.8p/50V

OSC32_OUT

OSC32_IN

Figure 4．Low frequency crystal circuit

## 1.2.4 JTAG circuit

JTAG circuit use Standard 20 pins connector as shown in the figure below.

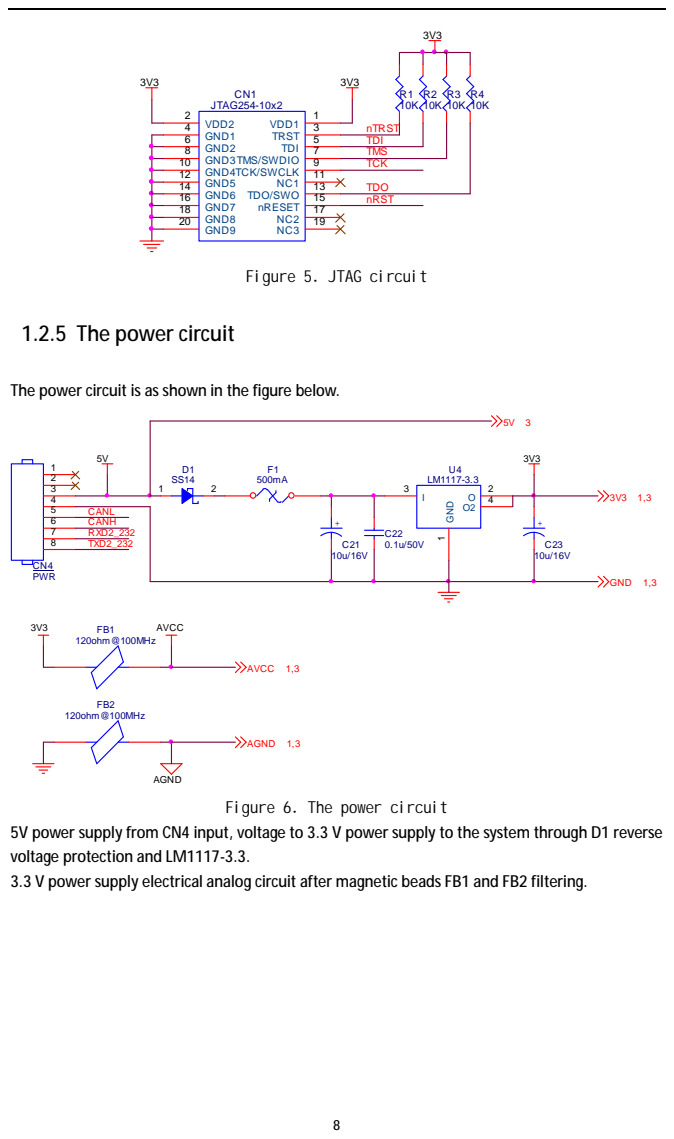
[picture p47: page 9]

The power circuit is as shown in the figure below.

Figure 6．The power circuit

5V power supply from CN4 input, voltage to 3.3 V power supply to the system through D1 reverse
voltage protection and LM1117-3.3.
3.3 V power supply electrical analog circuit after magnetic beads FB1 and FB2 filtering.

## 1.2.6 Indicator light circuit

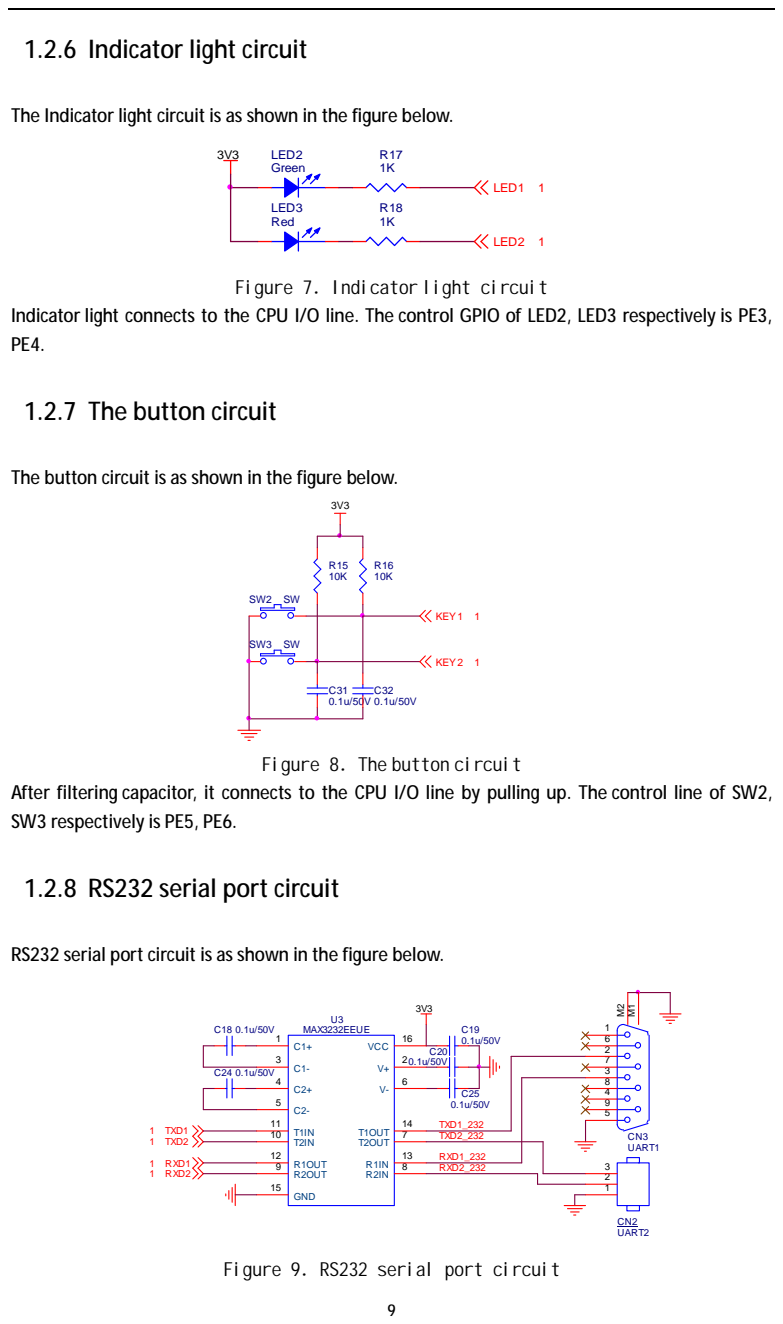
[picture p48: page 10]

The Indicator light circuit is as shown in the figure below.

Figure 7．Indicator light circuit

Indicator light connects to the CPU I/O line. The control GPIO of LED2, LED3 respectively is PE3,

The button circuit is as shown in the figure below.

Figure 8．The button circuit

After filtering capacitor, it connects to the CPU I/O line by pulling up. The control line of SW2,
SW3 respectively is PE5, PE6.

RS232 serial port circuit is as shown in the figure below.

Figure 9．RS232 serial port circuit

The electric level conversion between TTL and RS232 can be realized by SP3232; one serial port connects to the DB9 socket which can be directly connected to the PC serial port, another can connect to the terminal socket. The CPU resources are as shown in the figure:
The signal name | The processor port | Note
TXD1 | PC12
RXD1 | PD2
TXD2 | PC10
RXD2 | PC11

## 1.2.9 TTL serial portcircuit

TTL serial portcircuit is as shown in the figure below.

1 WF_IO1
1 WF_IO2

CN6
TTL_UART

1
2
3
4
5
6
7

1 WF_TXD

1 WF_RXD

3V3

1 WF_IO3

Figure 10．TTL serial port circuit
TTL serial port circuit is a circuit form the CPU to the terminal socket. The circuit includes 3 I/O control lines. The CPU resources are as shown in the figure:
The signal name | The processor port | Note
WF_RXD | PA1
WF_TXD | PA0
WF_IO1 | PE0
WF_IO2 | PE1
WF_IO3 | PE2

## 1.2.10RS485 circuit

RS485 circuit is as shown in the figure below.

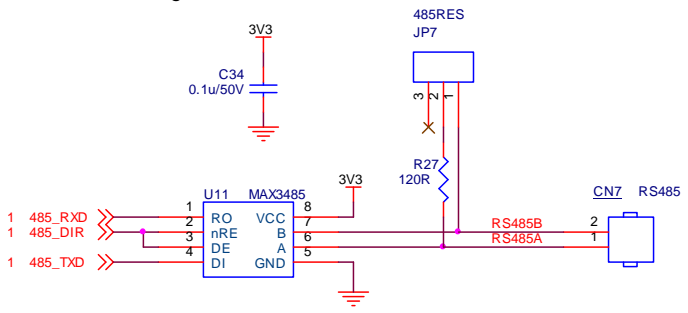
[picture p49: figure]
1 485_TXD; 1 485_DIR; 1 485_RXD; 485RES; MAX3485; nRE; GND; VCC

Figure 11．RS485 circuit
The electric level conversion between TTL and RS485 can be realized by SP3485. It can match impedance terminal resistance when JP7 1, 2 pin short circuit. The circuit driver chip can send and receive radio signal. The circuit driver chip is in a state of receiving signals at ordinary times, and in a state of sending signals only in need. After sending over, it comes to the receiving signal state immediately. The CPU resources are as shown in the figure:
The signal name | The processor port | Note
485_RXD | PA3
485_TXD | PA2
485_DIR | PB2

## 1.2.11CAN bus circuit

CAN bus circuit is as shown in the figure below.

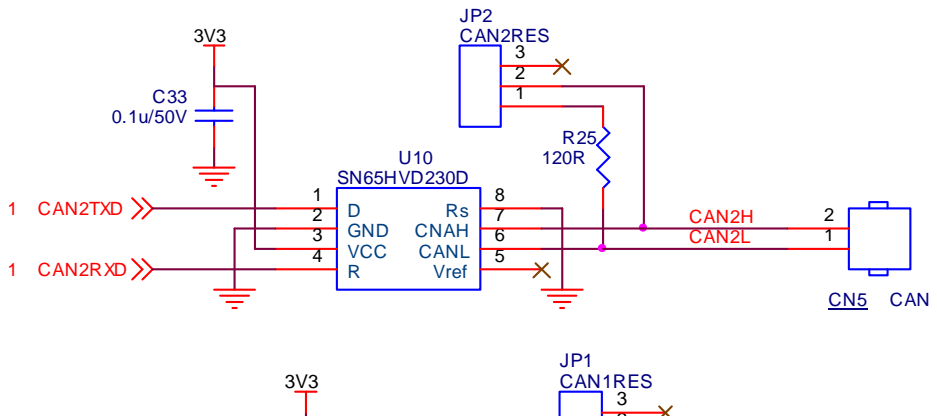
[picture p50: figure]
CN5 CAN; AN2TXD; 1 CAN2RXD; U10 SN65HVD230D; GND; VCC; Vref; CANL; CNAH; JP2 CAN2RES; CAN2L; CAN2H; JP1 CAN1RES 3
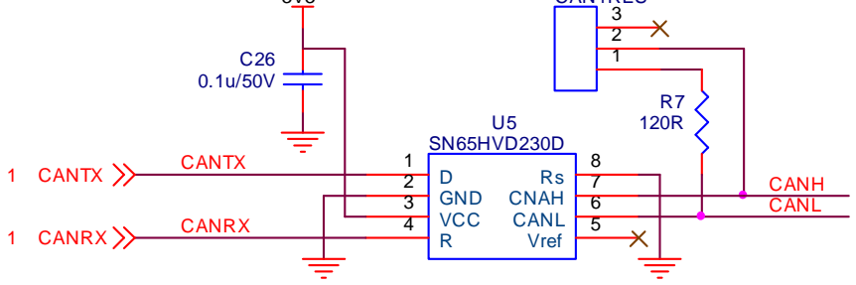
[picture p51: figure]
U5 SN65HVD230D; GND; VCC; Vref; CANL; CNAH; CANRX; CANTX; CANH 1 CANTX; 1 CANRX

Figure 12．CAN bus circuit
This system provides two CAN bus circuits; one is along with the input power plug-in board, another can use a separate plug-in board.CAN1 can match the terminal resistors by JP1; CAN 2 can match the terminal resistors by JP2.CAN bus circuit driver chip is the TI SN65HVD230. The CPU resources are as shown in the figure:
The signal name | The processor port | Note
CANTX | PB9
CANRX | PB8
CAN2TXD | PB6
CAN2RXD | PB5

## 1.2.12I2C interface circuit

I2C interface circuit is as shown in the figure below.

5V

I2CSDA 1 PWM4

1 PWM3 | I2CSCL

1 I2CINT

CN8I2C

1
2
3
4
5

Figure 13．I2C interface circuit

I2C interface circuit connects to the CPU I/O line directly. I2C interface can be used as the PWM3 or PWM4 interface. The CPU resources are as shown in the figure:
The signal name | The processor port | Note
SCL | PB10
SDA | PB11
INT | PA9

## 1.2.13TF card circuit

TF card circuit is as shown in the figure below.

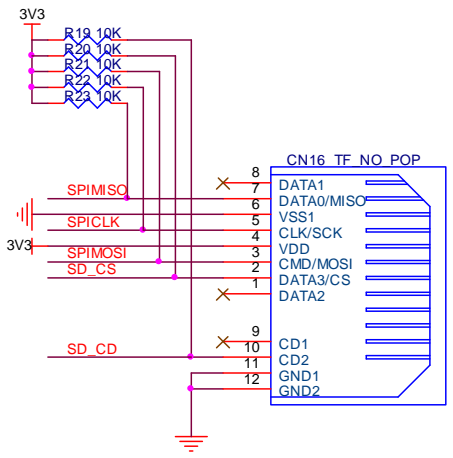
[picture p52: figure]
CN16 TF_NO_POP; DATA2; GND1; GND2; DATA1; DATA0/MISO; VSS1; CLK/SCK; VDD; CMD/MOSI; DATA3/CS; SPIMOSI; SPICLK; SPIMISO

Figure 14．TF cardcircuit
TF card circuit communicates by SPI bus. Each control single has the external pull-up resistor. The CPU resources are as shown in the figure:
The signal name | The processor port | Note
SPIMISO | PC2
SPIMOSI | PC3
SPICLK | PB13
SD_CS | PD3 | Select chip

## 1.2.14LCD module interface circuit

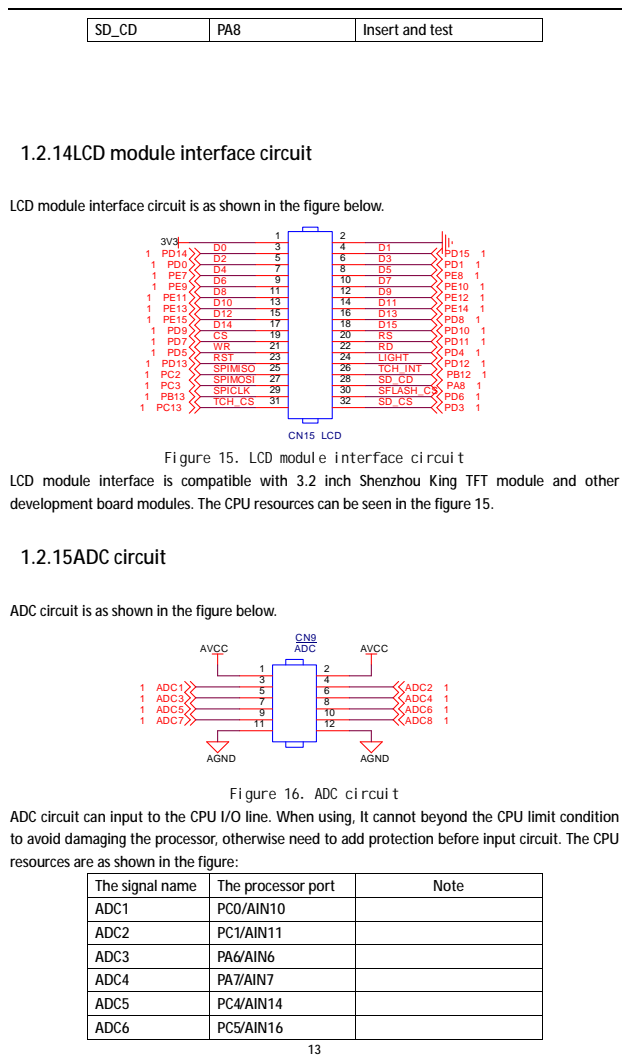
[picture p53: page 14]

LCD module interface circuit is as shown in the figure below.

Figure 15．LCD module interface circuit

LCD module interface is compatible with 3.2 inch Shenzhou King TFT module and other
development board modules. The CPU resources can be seen in the figure 15.

ADC circuit is as shown in the figure below.

ADC circuit can input to the CPU I/O line. When using, It cannot beyond the CPU limit condition
to avoid damaging the processor, otherwise need to add protection before input circuit. The CPU
resources are as shown in the figure:

The signal name | The processor port | Note
ADC1 | PC0/AIN10
ADC2 | PC1/AIN11
ADC3 | PA6/AIN6
ADC4 | PA7/AIN7
ADC5 | PC4/AIN14
ADC6 | PC5/AIN16

ADC7 | PB0/AIN8
ADC8 | PB1/AIN9

## 1.2.16DAC circuit

DAC circuit is as shown in the figure below.

CN14
DAC

1
2
3
4

AGND

1 DAC1
1 DAC2

Figure 17．DAC circuit
The DAC circuit can output directly, which can also be used as the ADC input circuit. The CPU resources are as shown in the figure:
The signal name | The processor port | Note
DAC1 | PA4/AOUT1/AIN4
DAC2 | PA5/AOUT2/AIN5

## 1.2.17PWM output circuit

PWM output circuit is as shown in the figure below.

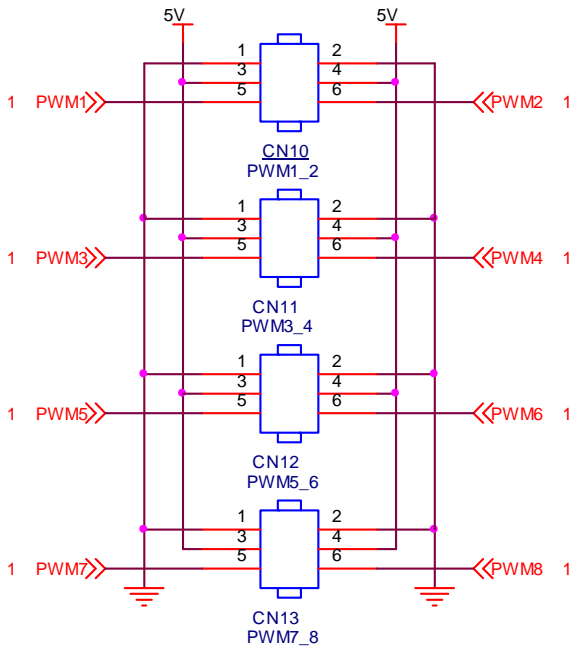
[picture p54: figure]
CN10 PWM1_2; CN11 PWM3_4; CN12 PWM5_6; CN13 PWM7_8; 1 PWM1; PWM2 1; 1 PWM3; PWM4 1; 1 PWM5; PWM6 1; 1 PWM7; PWM8 1

Figure 18．PWM output circuit
PWM output circuit can output directly, which can connect the steering-engine or other equipment. The CPU resources are as shown in the figure:

The signal name | The processor port | Note
PWM1 | PB14/T12CH1
PWM2 | PB15/T12CH2
PWM3 | PB10/T2CH3
PWM4 | PB11/T2CH4
PWM5 | PC6/T3CH1
PWM6 | PC7/T3CH2
PWM7 | PC8/T3CH3
PWM8 | PC9/T3CH4

## 2 The development environment introduction

Now there are so many ARM development environments. The MDK and IAR development environments are popular in china. The MDK development environment only supports the ARM7, ARM9 series and Cortex systems, while the IAR development environment can support the ARM11、Cortex-A9 systems. But the MDK development environment is more suitable for beginners.
There are some development environments based on GNU. Some of them need to pay.eg. TrueSTUDIO、RIDE. Some of them are free as emIDE.

## 2.1 MDK introduction

The RVMDK development environment is from KEIL in Germany. The name RVMDK is short for RealView MDK. RealView MDK integrates the industry's most advanced technology, including mu Vision4 integrated development environment and RealView compiler. The MDK development environment only supports the ARM7, ARM9 series and the latestCortex-M3、Cortex-M4.
The MDK development environment introduced is MDK ver4.5.

## 2.2 Establish a new project

Now what we introduced is to establish a new project named Demo in the RHF407_Examples folder in D disk. But you need to install MDK software and download to peripherals library stm32f4_dsp_stdperiph_lib. Zip from ST website and unzip to D disk root directory.

## 2.2.1 Establish a new project

The detailed step of establishing a new project: Start the’ Keil uVision4’, click the project menu ‘New uVision Project’ item, choose the directory ‘D:\ RHF407_Examples\Demo’ in the pop-up dialog box. If no directory in the dialog, you need to establish a new project named Demo in the dialog and click item ‘save ‘to close the dialog. As shown in the figure

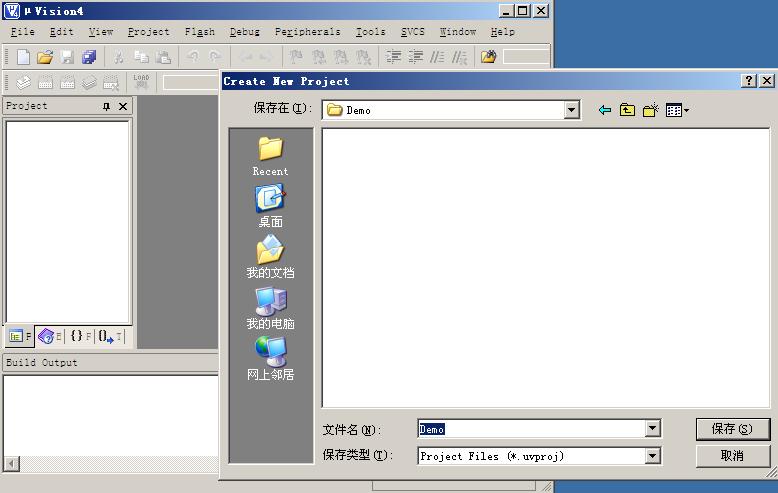
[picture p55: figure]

below:

Figure 19．Establish a new MDK project

## 2.2.2 Select the device

Select the device’ STM32F407VE ’ in the pop-up dialog box, click ‘OK ‘to close the dialog.

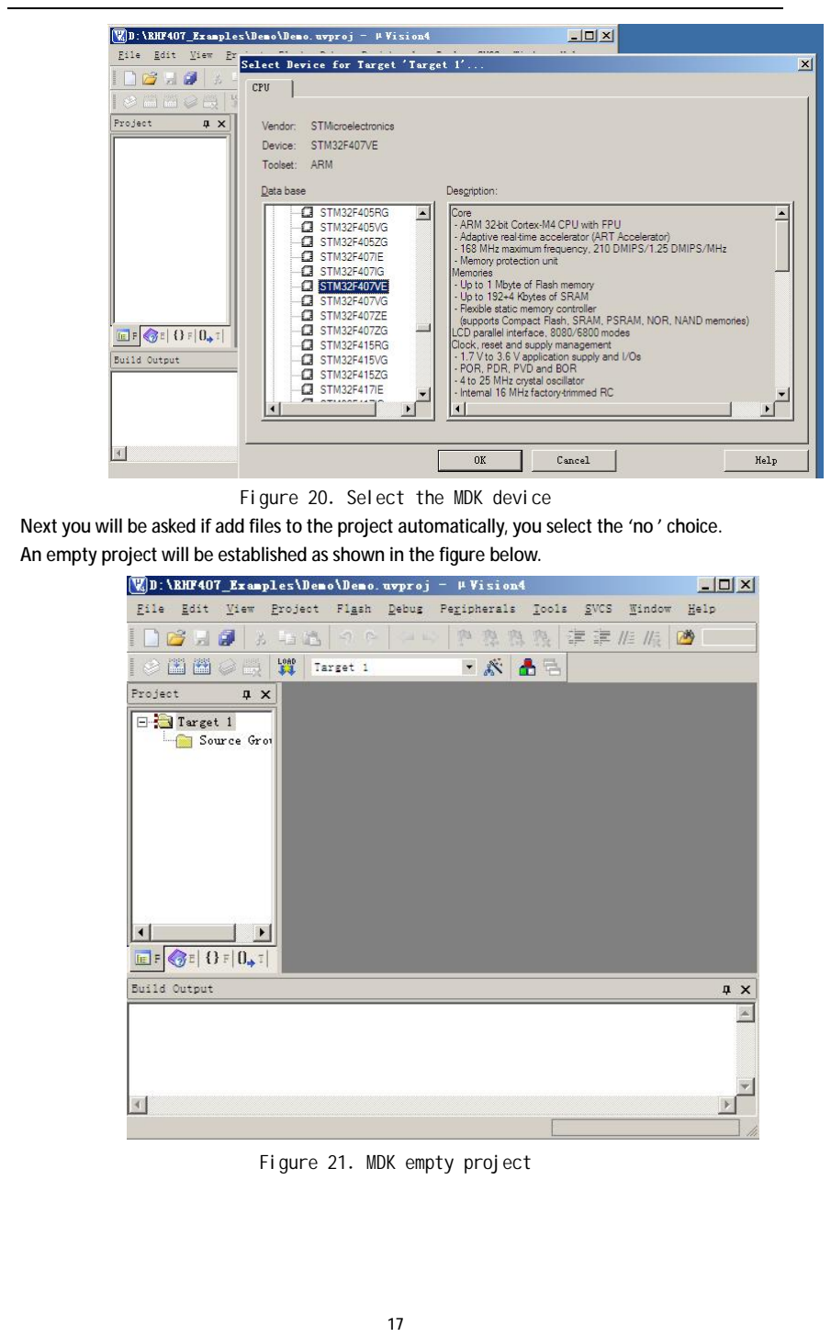
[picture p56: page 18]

Figure 20．Select the MDK device
Next you will be asked if add files to the project automatically, you select the ‘no ’ choice. An empty project will be established as shown in the figure below.

Figure 21．MDK empty project

## 2.2.3 Prepare the document

Copy the useful Libraries folder content to the Demo folder. You can delete unwanted files inside. Establish a new folder App in the Demo folder to hold the code files, and manually create the file App. C.

Click , you can manage the project files in the pop-up dialog box.
Double-click on the default entry in Project Targets and modify the name for the Debug.

Double-click on Source Group 1 in the groups and modify the name for the APP. Click the to set new CMSIS, Startup ,Library group in turn.
Choose the APP group, click Add files to add the file App.C in the APP folder.
Choose the CMSIS group, click Add files to add the file in the library Libraries\CMSIS\Device\ST\STM32F4xx\Source\Templates\system_stm32f4xx.c
Choose the Startup group, click Add files to add the file in the library :Libraries\CMSIS\Device\ST\STM32F4xx\Source\Templates\arm\startup_stm32f4xx.s
Choose the Library group, click Add files to add the standard peripherals driver file in the library :Libraries\STM32F4xx_StdPeriph_Driver\src
Click ‘OK ‘to close the dialog.

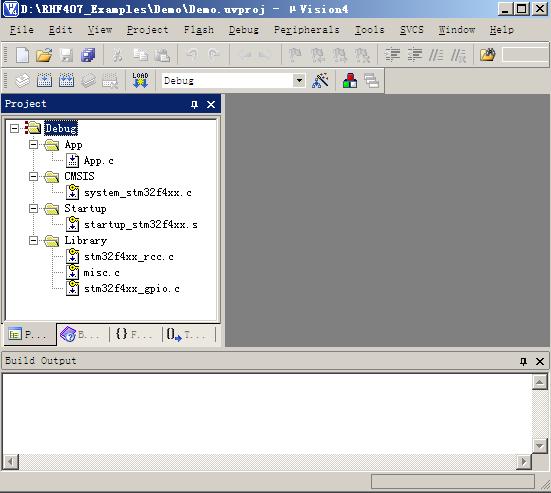
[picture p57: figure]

Figure 22．Add a file

## 2.2.4 Configure the project

Click , you can configure the project files in the pop-up dialog box.
Set the output file storage path in the Output page, click on Select Folder for Objects,add and select the new Folder bin.
Set the output file storage path in the Listing page, click on Select Folder for Listings,add and select the new Folder obj.
Setup compiler in C/C + + page, add macro definition USE_STDPERIPH_DRIVER,STM32F4XX after Define in order to use the official peripherals library. Add project header file path in the ‘Includes Paths’.

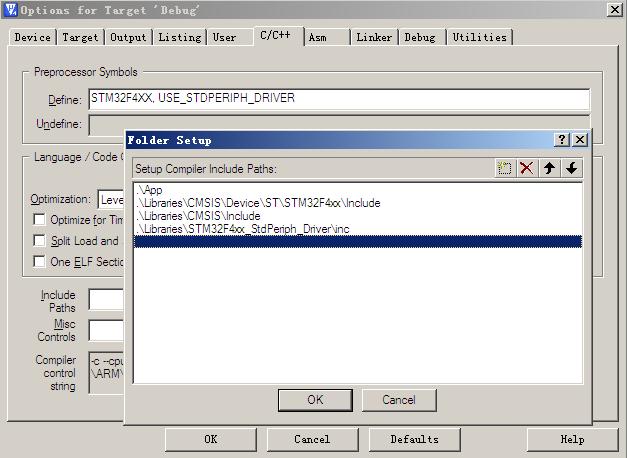
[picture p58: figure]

Figure 23．Configure the compiler
Configure the debugger in the Debug page, choose JLINK, Run to main, click Setting to set the JLINK debugger as shown in the figure below.

Figure 24．Configure the debugger

The dialog window to configure the ‘JLINK’ debugger in the figure above will be different when JLINK is not connected or target board has no electricity.
Configure the downloader in the Utilities page, choose ‘JLINK’, ‘Update Target before Debugging’. Click ‘Setting’ to set the JLINK downloader as shown in the figure below.
You need to add the corresponding device if no devices in the ‘Programming Algorithm’.

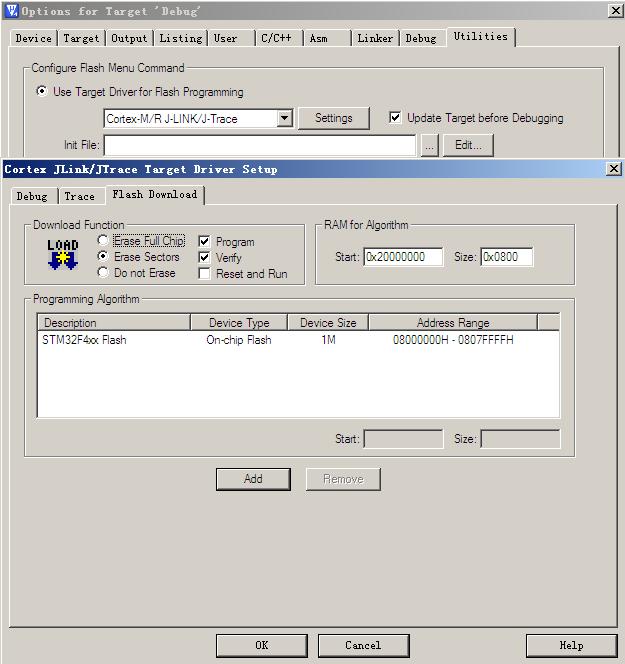
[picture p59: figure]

Figure 25．Configure the downloader
Now the project configuration is done.

## 2.2.5 Add the code

Although a basic project has been established, you need to add the codes because the file ‘App.c‘ is empty. For example, you can open the file and add the code as shown in figure.

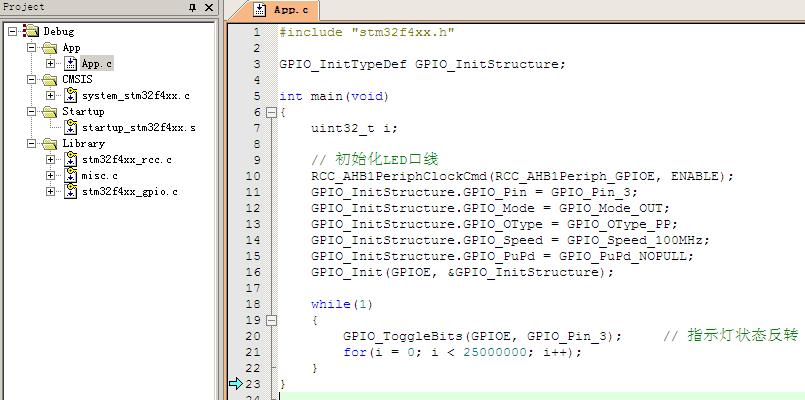
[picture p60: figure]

Figure 26．Add the code

## 2.2.6 Compile the project

Click , you can compile the project.
The output compiler information is as shown in the figure below.

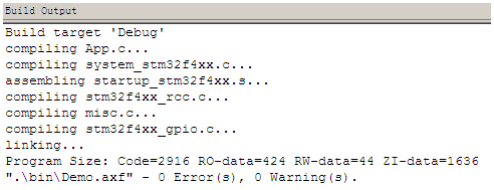
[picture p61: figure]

Figure 27．Output compiler information

## 2.2.7 Simulation debugging

Click to download the file into processor and start debugging. The program will execute to the entrance of the main function because of the settings ‘Run to the main’ in the debugger.

Click , the program will run at full speed. You can see that the green indicator light on the development board is flashing.

## 2.3 Starting process

It will execute start from the startup_stm32f4xx.s following code in the startup file when the system is reset.

Firstly you need to initialize System Init function in the executable file named ‘system_stm32f4xx.c including enable floating-point unit, clock, external SRAM, and interrupt to scale positioning, etc. And then began to implement the main function in the file named main.c

## 3 Basic routines

We designed a few necessary routine which contains more practical functionat ordinary times .The operation is basically based on the library function to avoid directly operate the registers. The question can be solved by searching online information.

## 3.1 Button control indicator light

The function of this routine is the following.
It will interrupt when two buttons on the board are pressed.Each key control an LED.The LED state will reverse to the corresponding contrary state when you press the button again.
Set a new folder ‘1. LED and Key’ in the routine catalogue.Copy the library to the folder.
Set a new folder Project\MDK-ARM,enter and set a new project named ‘project’
The directory structure is as shown in the figure below.

Because user program files in the routineis not much, so they are in the Project folder.

Considering some routines clock configuration will be different, in order not to damage the library files, the file ‘system_stm32f4xx. C’ is copied to the project folder and added to the project. Program files in the project folder are main.c、stm32f4xx_conf.h、stm32f4xx_it.c、 stm32f4xx_it.h、system_stm32f4xx.c
In this routine,other documents are the same as the official template in addition to the main c. From the frontcircuit description, we know the followings:
The indicator light is on when the indicator light line is in low electricity ,the indicator light is out when the indicator light line is in high electricity .It is in the low level state when button is pressed; and it is in the high level state when button is released.
At the time of programming, people like to begin with the main function, and gradually add the programs after a good framework. Obviously, an indicator light and the button anti-fuzzy initial function are needed,then you can add an empty infinite loop programs,.The code is as following. #include "stm32f4xx.h"
// main function
int main(void)
{
LedConfig();
KeyLineConfig();
while(1)
{
}
}
Light control belongs to typical GPIO port output applications. You need initialize before using according to the following process.
GPIO port line portclock
set mouth line mode
Implemented to define LED hardware resources,which can be easy to maintain and transplant. // LED light related definition
#define GPIO_LED | GPIOE | // LED port

#define RCC_GPIO_LED | RCC_AHB1Periph_GPIOE | // GPIO clock used by LED

#define LED1_PIN | GPIO_Pin_3 | // GPIO pin used by LED1

#define LED2_PIN | GPIO_Pin_4 | // GPIO pin used by LED2

Realize initialize function
// configure LED
void LedConfig(void)
{
GPIO_InitTypeDef GPIO_InitStructure;
RCC_AHB1PeriphClockCmd(RCC_GPIO_LED, ENABLE); | // enable clock
GPIO_InitStructure.GPIO_Pin = LED1_PIN|LED2_PIN; | // configure Pin pattern
GPIO_InitStructure.GPIO_Mode = GPIO_Mode_OUT; GPIO_InitStructure.GPIO_OType = GPIO_OType_PP; GPIO_InitStructure.GPIO_Speed = GPIO_Speed_100MHz; GPIO_InitStructure.GPIO_PuPd = GPIO_PuPd_NOPULL; GPIO_Init(GPIO_LED, &GPIO_InitStructure); // GPIO port initialize }
LED state reverse，it is state reverse of GPIO output state
// LED state reverse
void Led1Toggle(void)
{
GPIO_ToggleBits(GPIO_LED,LED1_PIN); | //LED1 status change

}
void Led2Toggle(void)
{
GPIO_ToggleBits(GPIO_LED,LED2_PIN); | //LED2 status change
}
Button is the typical GPIO input application, here it use break off, but it can check when it used on some occasion which needn’t quick response.
l enable GPIO port clock
l enable configure control clock
l configure GPIO pattern
l connect external interruption to GPIO
l Configure interrupt lines
l Enable interrupt and set up interrupt priority
definite hardware resource first
//button definition
#define GPIO_KEY | GPIOE | //KEY port

#define RCC_GPIO_KEY | RCC_AHB1Periph_GPIOE | // GPIO clock used by KEY

#define KEY1_PIN | GPIO_Pin_5 | // GPIO pin used by KEY1

#define KEY2_PIN | GPIO_Pin_6 | // GPIO pin used by KEY2

#define KEY1_PORT_SOURCE | EXTI_PortSourceGPIOE

#define KEY2_PORT_SOURCE | EXTI_PortSourceGPIOE

#define KEY1_PIN_SOURCE | EXTI_PinSource5

#define KEY2_PIN_SOURCE | EXTI_PinSource6

#define KEY1_EXTI_LINE | EXTI_Line5

#define KEY2_EXTI_LINE | EXTI_Line6

#define KEY1_EXTI_IRQN | EXTI9_5_IRQn

#define KEY2_EXTI_IRQN | EXTI9_5_IRQn

Write button initialize subprogram
// configure button
void KeyLineConfig(void)
{
EXTI_InitTypeDef EXTI_InitStructure; GPIO_InitTypeDef GPIO_InitStructure; NVIC_InitTypeDef NVIC_InitStructure;
// enable port clock
RCC_AHB1PeriphClockCmd(RCC_GPIO_KEY, ENABLE);
// enable system configure controller clock, external GPIO interrupt need RCC_APB2PeriphClockCmd(RCC_APB2Periph_SYSCFG, ENABLE);
//
GPIO_InitStructure.GPIO_Mode = GPIO_Mode_IN; GPIO_InitStructure.GPIO_PuPd = GPIO_PuPd_NOPULL;
GPIO_InitStructure.GPIO_Pin = KEY1_PIN | KEY2_PIN;
GPIO_Init(GPIO_KEY, &GPIO_InitStructure);
// connect interrupt line to Pin SYSCFG_EXTILineConfig(KEY1_PORT_SOURCE, KEY1_PIN_SOURCE); SYSCFG_EXTILineConfig(KEY2_PORT_SOURCE, KEY2_PIN_SOURCE); // set up interrupt line
EXTI_InitStructure.EXTI_Line = KEY1_EXTI_LINE; EXTI_InitStructure.EXTI_Mode = EXTI_Mode_Interrupt; EXTI_InitStructure.EXTI_Trigger = EXTI_Trigger_Falling;

EXTI_InitStructure.EXTI_LineCmd = ENABLE; EXTI_Init(&EXTI_InitStructure); EXTI_InitStructure.EXTI_Line = KEY2_EXTI_LINE; EXTI_Init(&EXTI_InitStructure);
// enable interrupt, set up interrupt priority NVIC_InitStructure.NVIC_IRQChannel = KEY1_EXTI_IRQN; NVIC_InitStructure.NVIC_IRQChannelPreemptionPriority = 0x0F; NVIC_InitStructure.NVIC_IRQChannelSubPriority = 0x0F; NVIC_InitStructure.NVIC_IRQChannelCmd = ENABLE; NVIC_Init(&NVIC_InitStructure); NVIC_InitStructure.NVIC_IRQChannel = KEY2_EXTI_IRQN; NVIC_Init(&NVIC_InitStructure);
}
attention，two keys trigger the same interrupt，and the design request that it can only control LED state after interrupt, this simple control can be done in the interrupt handling function. Interrupt response function is
//button interrupt handling function
void EXTI9_5_IRQHandler(void)
{
// check interrupt trigger source is button 1 or not
if( EXTI_GetITStatus(KEY1_EXTI_LINE) == SET )
{
Delay(10000); | // delay disappear shake
Led1Toggle(); | // indicator light 1 state reverse
EXTI_ClearITPendingBit(KEY1_EXTI_LINE); // clear interrupt line hang up bit
}
// check interrupt trigger source is button 2 or not
if( EXTI_GetITStatus(KEY2_EXTI_LINE) == SET )
{
Delay(10000);
Led2Toggle();
EXTI_ClearITPendingBit(KEY2_EXTI_LINE);
}
}
We use a disappear shake function above, it can use simple software. //delay function
void Delay(int _dly)
{
while(--_dly);
}
After compile and download, then run program，you can find two LED lights are all light up, because after initial because 口线 is on low voltage state after initialize, call below words, it is default out state when initialized. GPIO_SetBits(GPIO_LED, LED2_PIN |LED2_PIN)
Then, every time push the button1, it will lead LED1 state reverse, every time push the button2, it will lead LED2 state reverse.

## 3.2 Serial port (checking receive way )

Serial port communication is used a lot, the checking receive way is used in many console application. Here we will introduce DB9 standard serial port, for examples, it is OK to use standard straight line connect to PC serial port. Similar to previous, prepare the files, it is quickly to copy project. Files as follows:

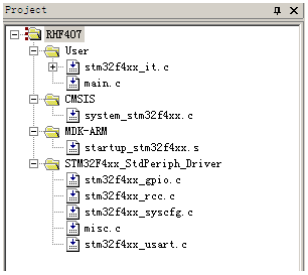
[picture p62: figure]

Add reference in the main.c file #include "stm32f4xx.h"
#include <stdio.h>

Finish main function
// main function
int main(void)
{
uint8_t rxchar;
ScomConfig();
printf("Please input char:\r\n");
while(1)
{
while(USART_GetFlagStatus(SCOM_BASE,USART_FLAG_RXNE) == RESET); rxchar = USART_ReceiveData(SCOM_BASE) & 0xFF; USART_SendData(SCOM_BASE, (uint8_t)rxchar);
}
}
Use standard print function to output character string after call ScomConfig() initialize serial port. Main cycle is waiting for serial port receive data, when data come, call function USART_Receive Data to receive data to rxchar，at last call USART_Send Data send the data out. We need to check and familiar function in stm32f4xx_usart.c，it is easy to know the purpose from function name.
Do not configure interrupt in the processing of serial port initial, because there is no use interrupt.
l Enable receive and send clock where the Pin port
l Enable present serial port, peripheral clock , serial port 1 and 6 is locate in APB2, others locate in APB1.
l Connect GPIO to serial port receive and send Pin
l Configure interface line mode
l Configure serial port mode, baud rate, initial bit and stop bit l Enable serial port
Definite hardware resource in front of file.
//serial definition
#define SCOM_BASE | UART5

#define SCOM_CLK | RCC_APB1Periph_UART5

#define SCOM_RCC_CMD | RCC_APB1

#define SCOM_TX_PIN | GPIO_Pin_12

#define SCOM_TX_GPIO_PORT | GPIOC

#define SCOM_TX_GPIO_CLK | RCC_AHB1Periph_GPIOC

#define SCOM_TX_SOURCE | GPIO_PinSource12

#define SCOM_TX_AF | GPIO_AF_UART5

#define SCOM_RX_PIN | GPIO_Pin_2

#define SCOM_RX_GPIO_PORT | GPIOD

#define SCOM_RX_GPIO_CLK | RCC_AHB1Periph_GPIOD

#define SCOM_RX_SOURCE | GPIO_PinSource2

#define SCOM_RX_AF | GPIO_AF_UART5

Write serial port initial function
// configure serial port
Void ScomConfig(void)
{
GPIO_InitTypeDef GPIO_InitStructure;
USART_InitTypeDef USART_InitStructure;
// enable RXD and TXD port peripheral clock
RCC_AHB1PeriphClockCmd(SCOM_TX_GPIO_CLK | SCOM_RX_GPIO_CLK, ENABLE);
// enable serial port peripheral clock
RCC_APB1PeriphClockCmd(SCOM_CLK, ENABLE);
// connect GPIO to serial port pin
GPIO_PinAFConfig(SCOM_TX_GPIO_PORT, SCOM_TX_SOURCE, SCOM_TX_AF); //
GPIO_PinAFConfig(SCOM_RX_GPIO_PORT, SCOM_RX_SOURCE, SCOM_RX_AF); // configure serial port TX as reuse function
GPIO_InitStructure.GPIO_OType = GPIO_OType_PP; GPIO_InitStructure.GPIO_PuPd = GPIO_PuPd_UP; GPIO_InitStructure.GPIO_Mode = GPIO_Mode_AF; GPIO_InitStructure.GPIO_Pin = SCOM_TX_PIN; GPIO_InitStructure.GPIO_Speed = GPIO_Speed_50MHz; GPIO_Init(SCOM_TX_GPIO_PORT, &GPIO_InitStructure); // configure serial port RX as reuse function GPIO_InitStructure.GPIO_Mode = GPIO_Mode_AF; GPIO_InitStructure.GPIO_Pin = SCOM_RX_PIN; GPIO_Init(SCOM_RX_GPIO_PORT, &GPIO_InitStructure);
// configure serial port
USART_InitStructure.USART_BaudRate = 115200; USART_InitStructure.USART_WordLength = USART_WordLength_8b; USART_InitStructure.USART_StopBits = USART_StopBits_1; USART_InitStructure.USART_Parity = USART_Parity_No; USART_InitStructure.USART_HardwareFlowControl
| = USART_HardwareFlowControl_None;
USART_InitStructure.USART_Mode = USART_Mode_Rx | USART_Mode_Tx;
USART_Init(SCOM_BASE, &USART_InitStructure);
// enable serial port
USART_Cmd(SCOM_BASE, ENABLE);
}
Now it can serial port receive and sent, but the former main function called standard print output function, it need to tell compiler how to output from serial port, and need to choose Use MicroLib in the Target page.

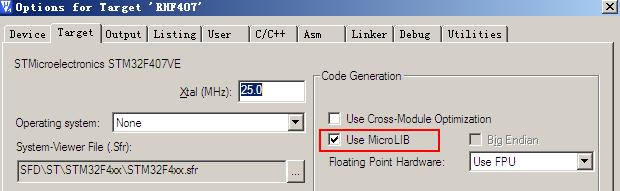
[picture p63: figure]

And realize below function //printf realized
int fputc(int ch, FILE *f)
{
USART_SendData(SCOM_BASE, (uint8_t)ch);
While (USART_GetFlagStatus(SCOM_BASE, USART_FLAG_TXE) == RESET); Return ch;
}
Compile and download，you can see below after implement in the HyperTerminal procedures.

Below is input echo bit.

## 3.3 serial port （interrupt receiving）

Modify on the former project, main cycle of main function do not need code, delete it. Print bit change point to make difference. Main function is as follows: // main function
int main(void)
{
ScomConfig();
printf("Uart in interrupt mode, please input char:\r\n"); While (1)
{
}
}
Add the serial port interrupt number definition
#define SCOM_IRQn | UART5_IRQn

Add interrupt initialize part in front of enable serial port when serial initializing.
// configure serial interrupt
NVIC_InitStructure.NVIC_IRQChannel = SCOM_IRQn; NVIC_InitStructure.NVIC_IRQChannelPreemptionPriority = 0; NVIC_InitStructure.NVIC_IRQChannelSubPriority = 1; NVIC_InitStructure.NVIC_IRQChannelCmd = ENABLE; NVIC_Init(&NVIC_InitStructure);
// enable serial port receiving interrupt
USART_ITConfig(SCOM_BASE, USART_IT_RXNE, ENABLE);
Now we need to have an interrupt service function, it will interrupt when receive a character every time, it will read this character in the function and then send it out.
// serial port interrupt service procedure serial interrupt service procedure
Void UART5_IRQHandler( void )
{
if ( USART_GetITStatus(SCOM_BASE, USART_IT_RXNE) != RESET )
{
Uint8_t rxchar;
rxchar = (USART_ReceiveData(SCOM_BASE) & 0xFF); USART_SendData(SCOM_BASE, rxchar);
}
}
attention：compared to checking，here the function is USART_GetITStatus，it is checking interrupt identification USART_IT_RXNE；while former function is USART_GetFlagStatus，it is checking state identification USART_FLAG_RXNE。 Compile and download，you can see below after running program in the HyperTerminal procedures.

## 3.4 Systick interrupt control LED

Systick aim to supply meter clock, many people use it to realize delay mode when have no control system. Because there are two 32 bite timer in the STM32F407, more flexible to delay, so here we use it as a common timer. Files are as follows:

Main function in the main.c file is as follows: // main function
int main(void)
{
// initialize LED
LedConfig();
// initialize Systick，beat is 1ms，if initialize fails, it will be an endless loop if (SysTick_Config(SystemCoreClock / 1000))
{
While (1);

}
While (1)
{
}
}
Definite LED hardware
//LED light definition
#define GPIO_LED | GPIOE | //LED port

#define RCC_GPIO_LED | RCC_AHB1Periph_GPIOE | //GPIO clock used by LED

#define LED1_PIN | GPIO_Pin_3 | // GPIO pin used by LED1

Initialize LED
// configure LED
Void LedConfig(void)
{
GPIO_InitTypeDef GPIO_InitStructure;
RCC_AHB1PeriphClockCmd(RCC_GPIO_LED, ENABLE); | // enable GPIO clock
GPIO_InitStructure.GPIO_Pin = LED1_PIN; | // configure pin mode
GPIO_InitStructure.GPIO_Mode = GPIO_Mode_OUT; GPIO_InitStructure.GPIO_OType = GPIO_OType_PP; GPIO_InitStructure.GPIO_Speed = GPIO_Speed_100MHz; GPIO_InitStructure.GPIO_PuPd = GPIO_PuPd_NOPULL;
GPIO_Init(GPIO_LED, &GPIO_InitStructure); | // GPIO initialize
}
LED state reverse function
//LED state reverse
void Led1Toggle(void)
{
GPIO_ToggleBits(GPIO_LED,LED1_PIN); | //LED1 state reverse
}
Now it still lack a Systick interrupt service function, this function is in the stm32f4xx_it.c, we can modify in there.
static unsigned int cnt = 0;
Extern void Led1Toggle(void);
Void SysTick_Handler(void)
{
cnt++;
If (cnt >= 500)
{
cnt = 0;
Led1Toggle ();
}
}

Because here we use LED reverse function, so we must add an external declaration in front of function.
Extern void Led1Toggle (void);
And because interrupts beat is 1 ms, if reversal LED state every time, frequency is 500 hz, the human eye can't be observed phenomenon, so add a global variable count, each interrupt accumulation, meter reset and inversion of the LED state after 500.
Compile and download, run program you can see LED2 will state revers every 1.5s.

## 3.5 DAC output

The project will configure output voltage by serial port, so it is simple to modify based on checking serial port.
Files need is as follows，Add the peripheral driver library file stm32f4xx_dac.c。

Add DAC initialize function in the main function. Configure the DAC voltage in the main cycle and trigger reverse, waiting serial port input “+”or“-” to modify output voltage.
// main function
int main(void)
{
Uint8_t rxchar;
Uint16_t dacdata = 0;
ScomConfig();
DacConfig();
printf("\r\nPress '+' or '-' change DAC output voltage.");
While (1)
{
// configure DAC1 and DAC2 output value, they are opposite DAC_SetChannel1Data(DAC_Align_12b_R, dacdata); DAC_SetChannel2Data(DAC_Align_12b_R, 4095 - dacdata); // trigger DAC reverse
DAC_SoftwareTriggerCmd(DAC_Channel_1, ENABLE); DAC_SoftwareTriggerCmd(DAC_Channel_2, ENABLE);
// print DAC1 output voltage
printf("\r\nDAC1 voltage= %dmV",(uint16_t)(3300*dacdata/4095));
// wait input serial bit to control output voltage while(USART_GetFlagStatus(SCOM_BASE,USART_FLAG_RXNE)==RESET ); rxchar = USART_ReceiveData(SCOM_BASE) & 0xFF;
if(rxchar == '+')
{
dacdata += 256;
}
else if(rxchar == '-')
{
dacdata -= 256;
}
dacdata %= 4096;
}
}

Initialize DAC
// configure DAC
void DacConfig(void)
{
GPIO_InitTypeDef GPIO_InitStructure;
DAC_InitTypeDef DAC_InitStructure;
// enable port clock
RCC_AHB1PeriphClockCmd(RCC_AHB1Periph_GPIOA, ENABLE); // enable DAC peripheral clock RCC_APB1PeriphClockCmd(RCC_APB1Periph_DAC, ENABLE); // configure interface line
GPIO_InitStructure.GPIO_Pin = GPIO_Pin_4 | GPIO_Pin_5;
GPIO_InitStructure.GPIO_Mode = GPIO_Mode_AN; GPIO_InitStructure.GPIO_PuPd = GPIO_PuPd_NOPULL; GPIO_Init(GPIOA, &GPIO_InitStructure);
// configure DAC channel
DAC_InitStructure.DAC_Trigger = DAC_Trigger_Software; DAC_InitStructure.DAC_WaveGeneration = DAC_WaveGeneration_None; DAC_InitStructure.DAC_OutputBuffer = DAC_OutputBuffer_Enable; DAC_Init(DAC_Channel_1, &DAC_InitStructure); DAC_Init(DAC_Channel_2, &DAC_InitStructure);
// enable DAC channel
DAC_Cmd(DAC_Channel_1, ENABLE);
DAC_Cmd(DAC_Channel_2, ENABLE);
}

Choose trigger mode when configurate DAC channel, enable output buffer. Compile and download, run program, we can use“+”or“-”to change DAC1 output voltage ，use multimeter to check DAC1 voltage on CN14.

### 3.6 ADC input

This text is based on the DAC output, it use ADC to gather DAC output voltage and send out from serial port. The project will be modify based on DAC output.

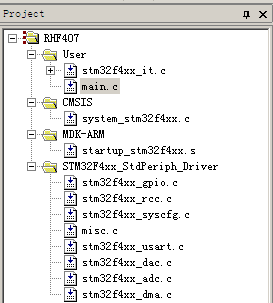
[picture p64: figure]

In DAC initializing, delate some code about DAC channel 2.Add ADC initialize call in the main function，software trigger and start ADC reverse.configure DAC output in the main cycle, Print DAC and ADC valotage from serial port after delay, waiting to modify DAC voltage. Code is as follows:
// main function
int main(void)
{
uint8_t rxchar;
uint16_t dacdata = 0;
uint32_t i;

ScomConfig();
DacConfig();
AdcConfig();
printf("\r\nPress '+' or '-' change DAC output voltage.");

// start ADC reverse
ADC_SoftwareStartConv(ADC1);

while(1)
{
// configure DAC output voltage and trigger reverse DAC_SetChannel1Data(DAC_Align_12b_R, dacdata); DAC_SoftwareTriggerCmd(DAC_Channel_1, ENABLE);

// delayed awaiting DAC input stable and ADC gathered well .

for(i = 0; i < 10000; i++);
// show DAC and ADC value
printf("\r\nVDAC = %dmV, VADC = %dmV", (uint16_t)(3300*dacdata / 4095), (uint16_t)(3300*adcvalue / 4095));

// wait setial port configurate output voltage. while(USART_GetFlagStatus(SCOM_BASE,USART_FLAG_RXNE)==RESET ); rxchar = USART_ReceiveData(SCOM_BASE) & 0xFF;
if(rxchar == '+')
{
dacdata += 256;
}
else if(rxchar == '-')
{
dacdata -= 256;
}
dacdata %= 4096;
}
}
ADC modules use DMA, configured to atomatic reverse mode, then it can work as design, and send sampling value assignment to global variable adcvalue. Definite ADC1 data register address and sampling value variable
#define ADC1_DR_ADDRESS ((uint32_t)0x4001204C) //ADC1 DR register address uint16_t adcvalue = 0;

when initialize ADC, use ADC1, its DMA can use flow 0’s channel 0 and channel 4 of DMA2，here we use channel 0. Code is as follows:
// configure ADC
void AdcConfig(void)
{
ADC_CommonInitTypeDef ADC_CommonInitStructure; DMA_InitTypeDef DMA_InitStructure; GPIO_InitTypeDef GPIO_InitStructure; ADC_InitTypeDef ADC_InitStructure;

// enable port peripheral and DMA2 clock

RCC_AHB1PeriphClockCmd(RCC_AHB1Periph_DMA2|RCC_AHB1Periph_GPIOC,ENABLE );
// enable ADC1 modual clock
RCC_APB2PeriphClockCmd(RCC_APB2Periph_ADC1, ENABLE);

// DMA2 flow 0 channel 0 configure
DMA_InitStructure.DMA_Channel = DMA_Channel_0; DMA_InitStructure.DMA_Memory0BaseAddr = (uint32_t)&adcvalue; DMA_InitStructure.DMA_PeripheralBaseAddr = (uint32_t)ADC1_DR_ADDRESS; DMA_InitStructure.DMA_DIR = DMA_DIR_PeripheralToMemory; DMA_InitStructure.DMA_BufferSize = 1;
DMA_InitStructure.DMA_PeripheralInc = DMA_PeripheralInc_Disable; DMA_InitStructure.DMA_MemoryInc = DMA_MemoryInc_Enable; DMA_InitStructure.DMA_PeripheralDataSize=DMA_PeripheralDataSize_HalfWord; DMA_InitStructure.DMA_MemoryDataSize = DMA_MemoryDataSize_HalfWord; DMA_InitStructure.DMA_Mode = DMA_Mode_Circular; DMA_InitStructure.DMA_Priority = DMA_Priority_High; DMA_InitStructure.DMA_FIFOMode = DMA_FIFOMode_Disable; DMA_InitStructure.DMA_FIFOThreshold = DMA_FIFOThreshold_HalfFull; DMA_InitStructure.DMA_MemoryBurst = DMA_MemoryBurst_Single; DMA_InitStructure.DMA_PeripheralBurst = DMA_PeripheralBurst_Single; DMA_Init(DMA2_Stream0, &DMA_InitStructure);

// enable DMA2 flow 0
DMA_Cmd(DMA2_Stream0, ENABLE);

// ------------------ADC relate configuration--------------------// GPIO configuration
GPIO_InitStructure.GPIO_Pin = GPIO_Pin_0; GPIO_InitStructure.GPIO_Mode = GPIO_Mode_AN; GPIO_InitStructure.GPIO_PuPd = GPIO_PuPd_NOPULL ; GPIO_Init(GPIOC, &GPIO_InitStructure);

// ADC common configuration ADC_CommonInitStructure.ADC_Mode = ADC_Mode_Independent; ADC_CommonInitStructure.ADC_Prescaler = ADC_Prescaler_Div2;

ADC_CommonInitStructure.ADC_DMAAccessMode = ADC_DMAAccessMode_Disabled;
ADC_CommonInitStructure.ADC_TwoSamplingDelay | =
ADC_TwoSamplingDelay_5Cycles; ADC_CommonInit(&ADC_CommonInitStructure);

// ADC channel 10 configuration
ADC_InitStructure.ADC_Resolution = ADC_Resolution_12b; ADC_InitStructure.ADC_ScanConvMode = DISABLE; ADC_InitStructure.ADC_ContinuousConvMode = ENABLE; ADC_InitStructure.ADC_ExternalTrigConvEdge = ADC_ExternalTrigConvEdge_None; ADC_InitStructure.ADC_DataAlign = ADC_DataAlign_Right; ADC_InitStructure.ADC_NbrOfConversion = 1;
ADC_Init(ADC1, &ADC_InitStructure);
ADC_RegularChannelConfig(ADC1, ADC_Channel_10, 1, ADC_SampleTime_3Cycles);

// enable DMA request
ADC_DMARequestAfterLastTransferCmd(ADC1, ENABLE);

// enable ADC1’s DMA
ADC_DMACmd(ADC1, ENABLE);

// enable ADC1
ADC_Cmd(ADC1, ENABLE);
}
Use dupont line to short-circuit DAC1 in the CN14 and ADC1 in the CN9.download and run program，use “+” or “-” to change DAC output voltage in the hyperTerminal ,you can see ADC voltage.as follows:

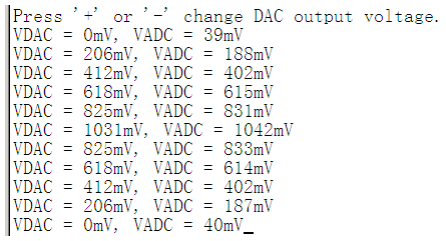
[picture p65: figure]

You can see ADC voltage will change as DAC voltage.

### 3.7 Basic timer interrupt

STM32 timer resource is rich and powerful, here we introduce a simple purpose,it is time interrupt, output the interrupt times in the interrupt service function. Compared to STM32F1xx ,STM32F4xx have two 32 bit timer, they are timer2 and timer5, here we use timer2.
Timer2 is locate in APB1 peripheral，when factional factor bigger than 2, input clock frenquency is two time APB1. Here the system clock frequency is 168MHz， APB1 factional is 4，so timer clock frequency is（168MHz/4）*2=84MHz。 Here we still use serial checking input to modify, files it need is

Add timer initial call in the main function, code is as follows: // main function
int main(void)
{
ScomConfig();
TimerConfig();

while(1)
{
}
}
Timer initial function is
// configure timer，use 32 bit timer 2
void TimerConfig(void)
{
NVIC_InitTypeDef | NVIC_InitStructure;
TIM_TimeBaseInitTypeDef TIM_TimeBaseStructure;

// enable timer peripheral clock RCC_APB1PeriphClockCmd(RCC_APB1Periph_TIM2, ENABLE);

// timer interrupt vector configuration
TIM_DeInit(TIM2);
NVIC_InitStructure.NVIC_IRQChannel = TIM2_IRQn; NVIC_InitStructure.NVIC_IRQChannelPreemptionPriority = 0; NVIC_InitStructure.NVIC_IRQChannelSubPriority = 1; NVIC_InitStructure.NVIC_IRQChannelCmd = ENABLE; NVIC_Init(&NVIC_InitStructure);

// timer parameter configuration TIM_TimeBaseStructure.TIM_Prescaler=(SystemCoreClock/2)/1000000-1; //clock1MHz
TIM_TimeBaseStructure.TIM_Period = 250000 - 1; | //
250ms
TIM_TimeBaseStructure.TIM_ClockDivision = TIM_CKD_DIV1; TIM_TimeBaseStructure.TIM_CounterMode = TIM_CounterMode_Up; TIM_TimeBaseInit(TIM2, &TIM_TimeBaseStructure);

// delate TIM2 overflow interrupt flag
TIM_ClearFlag(TIM2, TIM_IT_Update);

// timer overflow interrupt enable TIM_ITConfig(TIM2, TIM_IT_Update, ENABLE);

// when debugging, timer stop counting DBGMCU_APB1PeriphConfig(DBGMCU_TIM2_STOP, ENABLE);

// start counting
TIM_Cmd(TIM2, ENABLE);
}
In the above code，SystemCoreClock is system clock frequency, it is definited as168MHz in the system_stm32f4xx.c. call DBGMCU_APB1PeriphConfig, it can stop counting while debugging, otherwise it will comulative, then we will not see our expection.
Now there is lack of movement when interrupt the reponse function. As follows:
// timer interrupt service function

uint32_t cnt = 0;
void TIM2_IRQHandler(void)
{
if( TIM_GetITStatus(TIM2, TIM_IT_Update) != RESET ) {
// clear interrupt identification TIM_ClearITPendingBit(TIM2, TIM_IT_Update);

// processing
cnt++;
printf("\r\nCounter = %d", cnt);
}
}
Compile and download,run program, check it by HyperTerminal, you can find the intrrupt message will send out every 250ms.as follows:

### 3.8 Timer hardware delay

Here we will use timer2 to process hardware delay, for improve program running efficiency, byte operate register. Check project modify from serial port. The file project need is

Main function is
// main function
int main(void)
{
uint32_t cnt = 0;

ScomConfig();
TimerConfig();

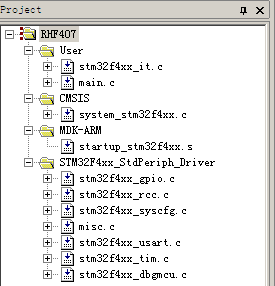
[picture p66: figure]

printf("\r\nTimer delay example.");

while(1)
{
printf("\r\nCounter = %d", cnt); cnt++;
TimerDelayMs(1000);
}
}
Initialize serial port and timer into main cycle, output delay time in the cycle, it will delay 1000ms every time.
Timer initialize function is
// configure function，use 32 bit timer2
void TimerConfig(void)
{
RCC->APB1ENR |= RCC_APB1ENR_TIM2EN; | // enable timer 2
peripheral clock
RCC->AHB1RSTR |= RCC_APB1RSTR_TIM2RST; | // reset timer 2
DBGMCU_APB1PeriphConfig(DBGMCU_TIM2_STOP, ENABLE); // timer stop counting

when debugging
}
In the initialize, Enable timer and configure stop counting function when debugging.
Millisecond delay procedure is
// ms grade delay function
void TimerDelayMs(uint32_t nms)
{
TIM2->PSC = 41999; | // timer clock frequency is 84MHz ，
fractional frequency is 2KHz
TIM2->CNT = 0;
TIM2->ARR = nms*2;
TIM2->CR1 = 0x01; | // start counting
while( 0 == (TIM2->SR) );
TIM2->CR1 = 0; | // stop counting
TIM2->SR = 0;
}
Because it is ms grade delay, so clock fractional frequency configured as clock frequency to solve 1Khz. Because fractional frequency coefficient is 0~65535，it is impossible to get 1KHz from 84MHz，but 2KHz is OK，so configure fractional frequency coefficient is（42000-1）。Because it is 0.5ms count pulse，so if want to get strong delay time, must delay microsecond multiply 2, assignment to timer automatic reset register, start counting. Then check state register all the time, until the state is not 0, it indicate that delay time is ready, stop counting and let state register return.
we can get microsecond delay subprogram after modify percale value. You can try if you have interest
After the procedure compiled and run, we can see plus 1 count value very second through HyperTerminal. As follows:

### 3.9 Timer generate PWM waveform

Here we use timer 3 generate 4 PWM waveforms. They are have same frequency but different duty cycle. Find a former project, it need this follow file:

Main function is simple，it only need to initialize PWM and get into endless cycle.
// main function
int main(void)
{
PwmConfig();

while(1)
{
}
}
PWM initialize
uint16_t CCR1_Val = 139;
uint16_t CCR2_Val = 279;
uint16_t CCR3_Val = 419;
uint16_t CCR4_Val = 559;
uint16_t PrescalerValue = 0; // configure PWM output
void PwmConfig(void)
{
TIM_TimeBaseInitTypeDef | TIM_TimeBaseStructure;
TIM_OCInitTypeDef | TIM_OCInitStructure;
GPIO_InitTypeDef | GPIO_InitStructure;

// timer clock enable
RCC_APB1PeriphClockCmd(RCC_APB1Periph_TIM3, ENABLE); // PWM function clock enable

RCC_AHB1PeriphClockCmd(RCC_AHB1Periph_GPIOC, ENABLE);

// configure PWM GPIO mode
GPIO_InitStructure.GPIO_Pin = GPIO_Pin_6 | GPIO_Pin_7 | GPIO_Pin_8 | GPIO_Pin_9;
GPIO_InitStructure.GPIO_Mode = GPIO_Mode_AF;
GPIO_InitStructure.GPIO_Speed = GPIO_Speed_100MHz; GPIO_InitStructure.GPIO_OType = GPIO_OType_PP;
GPIO_InitStructure.GPIO_PuPd = GPIO_PuPd_UP ; GPIO_Init(GPIOC, &GPIO_InitStructure);

// connect GPIO to timer
GPIO_PinAFConfig(GPIOC, GPIO_PinSource6, GPIO_AF_TIM3); GPIO_PinAFConfig(GPIOC, GPIO_PinSource7, GPIO_AF_TIM3); GPIO_PinAFConfig(GPIOC, GPIO_PinSource8, GPIO_AF_TIM3); GPIO_PinAFConfig(GPIOC, GPIO_PinSource9, GPIO_AF_TIM3);

/*----------------------------------------------------------------------
System clock frequency SystemCoreClock = 168MHz
APB1 clock frequency PCLK1 = SystemCoreClock / 4 = 42MHz Timer clock frequency TIM3CLK = 2 * PCLK1 = 84MHz

If timer count clock is 21MHz，prescale value is
Prescaler = (TIM3CLK / TIM3 counter clock) - 1 = ((SystemCoreClock /2) /21 MHz) - 1 = 3

If PWM waveform frequency is 30KHz，Automatically reinstall values ARR = (timer count clock frequency / 30000) - 1 = 699;

Every channel duty cycle：
Channel 1：CCR1/700 = 20%
Channel 2：CCR2/700 = 40%
Channel 3：CCR3/700 = 60%
Channel 4：CCR4/700 = 80%
----------------------------------------------------------------------*/

// calculate prescale value
PrescalerValue = (uint16_t) ((SystemCoreClock /2) / 21000000) - 1;

// timer configuration
TIM_TimeBaseStructure.TIM_Period = 699; TIM_TimeBaseStructure.TIM_Prescaler = PrescalerValue; TIM_TimeBaseStructure.TIM_ClockDivision = 0; TIM_TimeBaseStructure.TIM_CounterMode = TIM_CounterMode_Up; TIM_TimeBaseInit(TIM3, &TIM_TimeBaseStructure);

// PWM1 mode channel 1 configuration TIM_OCInitStructure.TIM_OCMode = TIM_OCMode_PWM1; TIM_OCInitStructure.TIM_OutputState = TIM_OutputState_Enable; TIM_OCInitStructure.TIM_Pulse = CCR1_Val; TIM_OCInitStructure.TIM_OCPolarity = TIM_OCPolarity_High; TIM_OC1Init(TIM3, &TIM_OCInitStructure); TIM_OC1PreloadConfig(TIM3, TIM_OCPreload_Enable);

// PWM1 mode channel 2 configuration TIM_OCInitStructure.TIM_OutputState = TIM_OutputState_Enable; TIM_OCInitStructure.TIM_Pulse = CCR2_Val;
TIM_OC2Init(TIM3, &TIM_OCInitStructure); TIM_OC2PreloadConfig(TIM3, TIM_OCPreload_Enable);

// PWM1 mode channel 3 configuration TIM_OCInitStructure.TIM_OutputState = TIM_OutputState_Enable; TIM_OCInitStructure.TIM_Pulse = CCR3_Val;
TIM_OC3Init(TIM3, &TIM_OCInitStructure); TIM_OC3PreloadConfig(TIM3, TIM_OCPreload_Enable);

// PWM1 mode channel 4 configuration TIM_OCInitStructure.TIM_OutputState = TIM_OutputState_Enable; TIM_OCInitStructure.TIM_Pulse = CCR4_Val;
TIM_OC4Init(TIM3, &TIM_OCInitStructure); TIM_OC4PreloadConfig(TIM3, TIM_OCPreload_Enable);

// allow automatic reinstall TIM_ARRPreloadConfig(TIM3, ENABLE);

// enable timer
TIM_Cmd(TIM3, ENABLE);
}
Compile, download and run, we use oscilloscope , and we can see the 30Khz waveform from PWM5~PWM on the CN12 and CN13.

### 3.10RTC

RTC real time clock is a individual unit, it can still work even CPU have no charge when there is spare battery. RTC is a real clock in the STM32F4xxnot just a counter to read minute and second. In this example it involves how to configure time and how to read time. Check receiving project modify according to serial port, files the project need is:

Main function is
// main function
int main(void)
{
uint32_t i;

ScomConfig();
RtcConfig();

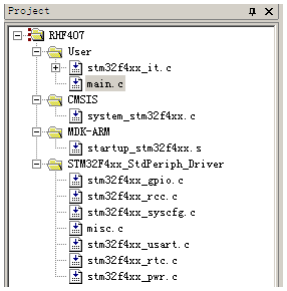
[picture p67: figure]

printf("Config RTC OK!\r\n");

while(1)
{
for(i = 0; i < 25000000; i++); // delay
RTC_TimeShow(); | // output present time
}
}
After initialize serial port and RTC, read delay some time and send RTC value. RTC reserve is located in the area, so long as has the backup battery, can after configured from processor cores have been run.Should check whether the configuration after each processor reset it, if you have configured a reconfiguration is generally do not. This can be realized by using backup registers that set a backup to the specified register after writing a specific value, read the register after reset, and the specific value as ever configuration RTC.
To protect RTC register value，the core will not be allowed to process RTC after reset.
RTC configure subprogram is
// configure RTC
uint32_t AsynchPrediv = 0, SynchPrediv = 0;
void RtcConfig(void)
{
// read backup region register 0, check if it is specific value 0x32F2 if (RTC_ReadBackupRegister(RTC_BKP_DR0) != 0x32F2)
{
printf("\r\nNot set RTC, now set it......");

// enable PWR clock
RCC_APB1PeriphClockCmd(RCC_APB1Periph_PWR, ENABLE);

// allow access to RTC
PWR_BackupAccessCmd(ENABLE);

// enable external low frequency crystal RCC_LSEConfig(RCC_LSE_ON);

// waiting external low frequency crystal stable while(RCC_GetFlagStatus(RCC_FLAG_LSERDY) == RESET);

// choose RTC clock is external low frequency crystal RCC_RTCCLKConfig(RCC_RTCCLKSource_LSE);

SynchPrediv = 0xFF;
AsynchPrediv = 0x7F;

// enable RTC clock
RCC_RTCCLKCmd(ENABLE);

// waiting RTC APB register synchronized RTC_WaitForSynchro();

// configure RTC data register and presclar coefficient RTC_InitStructure.RTC_AsynchPrediv = AsynchPrediv; RTC_InitStructure.RTC_SynchPrediv = SynchPrediv; RTC_InitStructure.RTC_HourFormat = RTC_HourFormat_24; if (RTC_Init(&RTC_InitStructure) == ERROR)
{
printf("\n\r RTC Prescaler Config failed.\n\r");
}

// configure time register
RTC_TimeRegulate();
}
else
{
printf("\n\r No need to configure RTC....\n\r");

// enable PWR clock
RCC_APB1PeriphClockCmd(RCC_APB1Periph_PWR, ENABLE);

// allow access RTC
PWR_BackupAccessCmd(ENABLE);

// waiting APB register synchronized

RTC_WaitForSynchro();
}
}
When you do not have configured RTC before, Call RTC_TimeRegulate()to configurate present time，code is as follows:
// reture to the time that user input
void RTC_TimeRegulate(void)
{
uint32_t tmp_hh = 0xFF, tmp_mm = 0xFF, tmp_ss = 0xFF;

printf("\n\r==============Time Settings=====================================\n\r"); RTC_TimeStructure.RTC_H12 = RTC_H12_AM; printf(" Please Set Hours:\n\r");
while (tmp_hh == 0xFF)
{
tmp_hh = USART_Scanf(23);
RTC_TimeStructure.RTC_Hours = tmp_hh; }
printf(" %0.2d\n\r", tmp_hh);

printf(" Please Set Minutes:\n\r"); while (tmp_mm == 0xFF)
{
tmp_mm = USART_Scanf(59);
RTC_TimeStructure.RTC_Minutes = tmp_mm; }
printf(" %0.2d\n\r", tmp_mm);

printf(" Please Set Seconds:\n\r"); while (tmp_ss == 0xFF)
{
tmp_ss = USART_Scanf(59);
RTC_TimeStructure.RTC_Seconds = tmp_ss; }
printf(" %0.2d\n\r", tmp_ss);

/* Configure the RTC time register */ if(RTC_SetTime(RTC_Format_BIN, &RTC_TimeStructure) == ERROR) {
printf("\n\r>> !! RTC Set Time failed. !! <<\n\r");
}
else
{
printf("\n\r>> !! RTC Set Time success. !! <<\n\r"); RTC_TimeShow();
/* Indicator for the RTC configuration */ RTC_WriteBackupRegister(RTC_BKP_DR0, 0x32F2); }

tmp_hh = 0xFF;
tmp_mm = 0xFF;
tmp_ss = 0xFF;
}
This subprogram just reminder user input time, USART_Scanf()is realize serial port input data receive and analysis.
In main function cycle call RTC_TimeShow() to read and send present time message, code is as follows:
// serial port shows present time
void RTC_TimeShow(void)
{
// read present time
RTC_GetTime(RTC_Format_BIN, &RTC_TimeStructure); // send time message
printf("\n\r Time is : %0.2d:%0.2d:%0.2d", RTC_TimeStructure.RTC_Hours, RTC_TimeStructure.RTC_Minutes,
RTC_TimeStructure.RTC_Seconds);
}
Compile and download，you can use HyperTerminal to configure time after the program run well, please attention, the date must be double-digit. Please see below:

### 3.11 CAN network

CAN is a popular bus, usually used in car and industry. This board have two individual CAN bus port, communicate with each other，this example is realize communicate in both CAN port, and send data from CAN port serial port.

Configure baud rate before use CAN, Especially the timing parameters can't be too casual, had better be in accordance with the standards。According to their own need to configure the acceptance filter, there can be multiple acceptance filter. Data reception generally use the interrupt way, not so many requirements on send , only need to pay attention to the message ID, message type (standard frame or extended frame, data frame or remote frame), data length, and data will be send In this example launched the first packet of data to send by CAN1, send data only one byte 0;CAN2 will add 1 and return data after receiving the message, CAN1will add 1 and return data after receiving the message, So keep going. Every time in the CAN interrupt handle function will send received message to the serial port and time delay.
This project can modify according to serial check receiving project. File need is as follows:

We need to definite a send packet variable and a receive packet for the two CAN port in the main.c file.

// main function
int main(void)
{
// initialization serial port and CAN port ScomConfig();
CanConfig();

// ready to send text message TxMessage1.StdId = 0;
TxMessage1.ExtId = SCAN2_MSG_ID; TxMessage1.RTR = CAN_RTR_DATA; TxMessage1.IDE = CAN_ID_EXT; TxMessage1.DLC = 1;
TxMessage1.Data[0] = 0;

TxMessage2.StdId = 0;
TxMessage2.ExtId = SCAN1_MSG_ID; TxMessage2.RTR = CAN_RTR_DATA; TxMessage2.IDE = CAN_ID_EXT; TxMessage2.DLC = 1;
TxMessage2.Data[0] = 0;

// send initial text message, start to transmit CAN_Transmit(SCAN1_BASE, &TxMessage1);

while(1)
{
}
}

define the message IDs received by CAN1 and CAN2
#define SCAN1_MSG_ID | 0x0001

#define SCAN2_MSG_ID | 0x0002

define CAN hardware resources
// CAN port defination
// SCAN1
#define SCAN1_BASE | CAN1

#define SCAN1_CLK | RCC_APB1Periph_CAN1

#define SCAN1_RX_PIN | GPIO_Pin_8

#define SCAN1_TX_PIN | GPIO_Pin_9

#define SCAN1_GPIO_PORT | GPIOB

#define SCAN1_GPIO_CLK | RCC_AHB1Periph_GPIOB

#define SCAN1_AF_PORT | GPIO_AF_CAN1

#define SCAN1_RX_SOURCE | GPIO_PinSource8

#define SCAN1_TX_SOURCE | GPIO_PinSource9

#define SCAN1_RX0_IRQn | CAN1_RX0_IRQn

// SCAN2
#define SCAN2_BASE | CAN2

#define SCAN2_CLK | RCC_APB1Periph_CAN2

#define SCAN2_RX_PIN | GPIO_Pin_5

#define SCAN2_TX_PIN | GPIO_Pin_6

#define SCAN2_GPIO_PORT | GPIOB

#define SCAN2_GPIO_CLK | RCC_AHB1Periph_GPIOB

#define SCAN2_AF_PORT | GPIO_AF_CAN2

#define SCAN2_RX_SOURCE | GPIO_PinSource5

#define SCAN2_TX_SOURCE | GPIO_PinSource6

#define SCAN2_RX0_IRQn | CAN2_RX0_IRQn

initialize the two CAN buses //configure CAN
void CanConfig(void)
{
NVIC_InitTypeDef NVIC_InitStructure; GPIO_InitTypeDef GPIO_InitStructure;
CAN_InitTypeDef | CAN_InitStructure;
CAN_FilterInitTypeDef CAN_FilterInitStructure;

// Configurate two CAN’s interrupt channel NVIC_InitStructure.NVIC_IRQChannel = CAN1_RX0_IRQn; NVIC_InitStructure.NVIC_IRQChannelPreemptionPriority = 0x0; NVIC_InitStructure.NVIC_IRQChannelSubPriority = 0x0; NVIC_InitStructure.NVIC_IRQChannelCmd = ENABLE; NVIC_Init(&NVIC_InitStructure); NVIC_InitStructure.NVIC_IRQChannel = CAN2_RX0_IRQn; NVIC_Init(&NVIC_InitStructure);

/ /Enable port GPIO Clock
RCC_AHB1PeriphClockCmd(SCAN1_GPIO_CLK, ENABLE);

// link CAN with Pin
GPIO_PinAFConfig(SCAN1_GPIO_PORT, SCAN1_RX_SOURCE, SCAN1_AF_PORT); GPIO_PinAFConfig(SCAN1_GPIO_PORT, SCAN1_TX_SOURCE, SCAN1_AF_PORT); GPIO_PinAFConfig(SCAN2_GPIO_PORT, SCAN2_RX_SOURCE, SCAN2_AF_PORT); GPIO_PinAFConfig(SCAN2_GPIO_PORT, SCAN2_TX_SOURCE, SCAN2_AF_PORT);

// configure GPIO Pin
GPIO_InitStructure.GPIO_Pin | =
SCAN1_RX_PIN|SCAN1_TX_PIN|SCAN2_RX_PIN|SCAN2_TX_PIN; GPIO_InitStructure.GPIO_Mode = GPIO_Mode_AF;
GPIO_InitStructure.GPIO_Speed = GPIO_Speed_50MHz; GPIO_InitStructure.GPIO_OType = GPIO_OType_PP; GPIO_InitStructure.GPIO_PuPd = GPIO_PuPd_UP; GPIO_Init(SCAN1_GPIO_PORT, &GPIO_InitStructure);

// enable CAN peripheral clock

RCC_APB1PeriphClockCmd(SCAN1_CLK | SCAN2_CLK, ENABLE);

// CAN register restore defaults
CAN_DeInit(SCAN1_BASE);
CAN_DeInit(SCAN2_BASE);

// configure CAN node cell CAN_InitStructure.CAN_TTCM = DISABLE; CAN_InitStructure.CAN_ABOM = DISABLE; CAN_InitStructure.CAN_AWUM = DISABLE; CAN_InitStructure.CAN_NART = DISABLE; CAN_InitStructure.CAN_RFLM = DISABLE; CAN_InitStructure.CAN_TXFP = DISABLE; CAN_InitStructure.CAN_Mode = CAN_Mode_Normal; CAN_InitStructure.CAN_SJW = CAN_SJW_1tq;

// Set baud rate
CAN_InitStructure.CAN_BS1 = CAN_BS1_6tq; CAN_InitStructure.CAN_BS2 = CAN_BS2_8tq; CAN_InitStructure.CAN_Prescaler = 2; CAN_Init(SCAN1_BASE, &CAN_InitStructure); CAN_Init(SCAN2_BASE, &CAN_InitStructure);

//CAN1 acceptance filter structure CAN_FilterInitStructure.CAN_FilterNumber = 0; CAN_FilterInitStructure.CAN_FilterMode = CAN_FilterMode_IdMask; CAN_FilterInitStructure.CAN_FilterScale = CAN_FilterScale_32bit; CAN_FilterInitStructure.CAN_FilterIdHigh =
(( ( uint32_t )SCAN1_MSG_ID << 3) & 0xFFFF0000) >> 16; CAN_FilterInitStructure.CAN_FilterIdLow =
((( uint32_t)SCAN1_MSG_ID<<3)|CAN_ID_EXT| CAN_RTR_DATA) & 0xFFFF; CAN_FilterInitStructure.CAN_FilterMaskIdHigh = (( ( uint32_t )0xFF << 3) & 0xFFFF0000) >> 16; //0xFFFF; CAN_FilterInitStructure.CAN_FilterMaskIdLow =
(( ( uint32_t )0xFF << 3) | CAN_ID_EXT | CAN_RTR_DATA) & 0xFFFF; //0xFFFF;
CAN_FilterInitStructure.CAN_FilterFIFOAssignment = 0;

CAN_FilterInitStructure.CAN_FilterActivation = ENABLE; CAN_FilterInit(&CAN_FilterInitStructure);

//CAN2 acceptance filter structure CAN_FilterInitStructure.CAN_FilterNumber = 14; CAN_FilterInitStructure.CAN_FilterIdHigh =
(( ( uint32_t )SCAN2_MSG_ID << 3) & 0xFFFF0000) >> 16; CAN_FilterInitStructure.CAN_FilterIdLow =
(( ( uint32_t )SCAN2_MSG_ID << 3) | CAN_ID_EXT | CAN_RTR_DATA) &
0xFFFF;
CAN_FilterInit(&CAN_FilterInitStructure);

// enable FIF00 message suspend and interrupt CAN_ITConfig(SCAN1_BASE, CAN_IT_FMP0, ENABLE);
CAN_ITConfig(SCAN2_BASE, CAN_IT_FMP0, ENABLE);
}
Attention shall be paid to baud rate and acceptance filter configuration during initialization. System Test describes the computational formula of baud rate as follows:

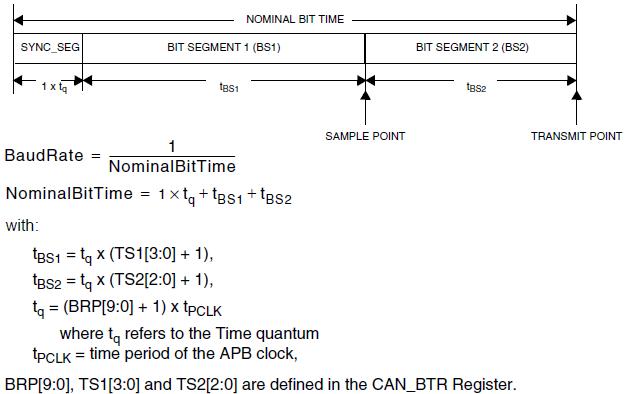
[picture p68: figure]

In a simple way:

In this case, the system clock is set as 120 MHz in file system_stm32f4xx.c, CANAPB1 peripheral clock shows four frequency of system clock, which equals to 30MHz. If the frequency factor is two, according to the formula above, baud rate can be calculated as:

Acceptance filters of CAN1 and CAN2 are set to receive previously defined ID message and extend teledata.
// CAN1 interrupt receive function
void CAN1_RX0_IRQHandler(void)
{
uint32_t i;
// | read all FIFO data
| while (CAN_MessagePending(SCAN1_BASE, CAN_FIFO0))
{
| CAN_Receive(SCAN1_BASE, CAN_FIFO0, &RxMessage1);
| for(i = 0; i < 25000000; i++);
| TxMessage1.Data[0] = RxMessage1.Data[0] + 1;
| printf("\r\n CAN1 recv 0x%02x", RxMessage1.Data[0]);
| CAN_Transmit(SCAN1_BASE, &TxMessage1);
}
}

// CAN2 interrupt receive function void CAN2_RX0_IRQHandler(void) {
| uint32_t i;
| // read all FIFO data
| while (CAN_MessagePending(SCAN2_BASE, CAN_FIFO0))
{
| CAN_Receive(SCAN2_BASE, CAN_FIFO0, &RxMessage2);
| for(i = 0; i < 25000000; i++);
| TxMessage2.Data[0] = RxMessage2.Data[0] + 1;
| printf("\r\n CAN2 recv 0x%02x", RxMessage2.Data[0]);
| CAN_Transmit(SCAN2_BASE, &TxMessage2);
}
}
Short out pin 1, 2 of JP1 and JP2, and connect CAN buses of CN4 and CN5,then compile download and run, the following will show on the HyperTerminal:

The first data package was sent by CAN1, so the first line shows CAN2 receiving message.

## 4 Chassis control routine

### 4.1 Control protocol introduction

Platform motor drive can control 4 motors at most, while users need 2 commands only, which provide control command based on serial port and CAN bus.

## 4.1.1 CAN bus control command

CAN bus data package adopt extend date frame in unification, dividing ID into address, command, and sub command. When default of baud rate is 500Kbps, the address will be 0x40.

Each CAN data package could transmit 8 byte data at most, multibyte data(such as floating-point data) array in data area in form of little end structure(low-order bytes stay at low-order address).

### 4.1.1.1 User-defined motor speed

Subcomman d; Function code; addres s; Data 0; Data 1; Data 2; Data 3; Data 4; Data 5; Data 6; Data 7

0 | 0x29 | 0x40 | Motor 1 speed Motor 2 speed Motor 3 speed Motor 4 speed
Direct control the rotational linear speed of each wheel. Motor speed is a 16
bits integer, 0.1mm/s as the unit. For example, 1000 stands for 0.1m/s of motor
speed.

### 4.1.1.2 triaxial speed control

Subcomman d; Function code; addres s; Data 7; X directional; speed; Y directional speed; autorotation rate; Reserve, 0

Data 0 | Data 1 | Data 2 | Data 3 | Data 4 | Data 5 | Data

Direct control the rotational linear speed of each wheel. Motor speed is a 16 bits integer, 0.1mm/s as the unit. For example, 1000 stands for 0.1m/s of motor speed.

X and Y directional speed that control platform’s movement and autorotation rate. Unit speed is 0.1mm/s for both X and Y directional speed, and autorotation rate is 0.0001rad/s, setting reserved bits to be zero. The speeds in three directions are 16 bits integers.

## 4.1.2 Serial port control command

Serial port command is transmitted in form of binary system.
Start characte r | Device type | Device address | Functio n code | Data length | Data area(N) | CRC check | End characte r
0xAA | | | | | | （L，H） | 0x0D
Explanation of each area:
Start character: One byte. the start of a data package. The fixed format is 0xAA. Device type: 0x51.
Device address: 0x40。
Function code: one byte, expressing function command. Users get access to the device, with function code provided by the manufacturer, in accordance with specified format.
Data length: one byte, expressing number of bits followed in the valid data area. Number of bits ranging from 0 to 255.
Data area: N bytes, expressing valid data, length is same with number of bits defined by data length. There is no data area when the data length is zero. Multisystem data array in form of little end.
CRC check: 2 bytes. 16 bits CRC check value of all characters from start character to end character in the data area.
End character: one bit, expressing the end of data package. The fixed format is 0x0D
Serial port data package shall be continuously transmitted after all the data are ready. In this way, it can be avoided that receiver keep waiting for unfinished data package while sender is under abnormal condition. This transition process cannot pause for too long, otherwise the receiver would mistake for finished transition, thus lead to error during parsing the data package.
Serial port communication parameters are “9600, N, 8, 1”.

### 4.1.2.1 user-defined motor speed

Function code; Data length; Data 0; Data 1; Data 2; Data 3; Data 4; Data 5; Data 6; Data 7; Motor1 speed; Motor2 speed; Motor3 speed; Motor4 speed

The description for above is same with command of CAN protocol.

### 4.1.2.2 three directional speed control

Function code; Data length; Data 7

Data 0 | Data 1 | Data 2 | Data 3 | Data 4 | Data 5 | Data
0x2A | 8 | X directional speed Y directional speed autorotation rate | Reserve, 0
The description for above is same with command of CAN protocol.

### 4.2 Routine introduction

## 4.2.1 Routine function

In this routine, RHF407 development board will be used and together with CAN bus command and serial port command to complete two motions control. Users can choose communication interface according to the control system described later, then compile and download the project.
After power on and user pressed the button SW2, platform will conduct rectangle and diagonal movement sequence, which can be realized by calling three directional speed control command. When the button SW3 is pressed, platform will rotate in situ, which can be realized by callig user-defined motor speed.
If the parameters were examined to be error when calling command after SW2 or SW3 is pressed, LED 3 will be lightened. LED3 is in off status when parameters are right.

## 4.2.2 Set up project

According to the function description above, visible-to-user hardware resources are indicator lights, buttons, and serial ports and CAN bus. Delayer and timer will also be used in some normal situations.
Firstly plan directory structure for project, and create some empty file(drv_ or app_ prefixal files).

Operation project folder named as RHF407 Demo, which includes all the codes needed for the whole firmware project.
l RHF407 Demo_Fw1.0: firmware source code project folder n App: user program, usually function code
u Inc: user program header file
l stm32f4xx_conf.h
l stm32f4xx_it.h
l app_protocal_uart.h
l app_protocal_can.h
l app_robot_control.h
u Src:user program C file
l app_main.c
l app_robot_control.c
l app_protocal_uart.c
l app_protocal_can.c
l stm32f4xx_it.c
n Driver: drive program writed by user u Inc: drive program header file l drv_button.h
l drv_can.h
l drv_delay.h
l drv_led.h
l drv_timer.h
l drv_uart.h
u Src: drive program C file l drv_button.c
l drv_can.c
l drv_delay.c
l drv_led.c
l drv_timer.c
l drv_uart.c
n Libraries: office libraries file. Delete needless file for project, and move stm32f4xx.h and system_stm32f4xx.h to CMSIS\Include, delete empty folder. Sine and cosine calculation function in DSP file will be used, so copy arm_cos_f32.c and arm_sin_f32.c to Libraries\CMSIS.
n Startup: start-up file, copy system_stm32f4xx.c and startup_stm32f4xx.s from official liabraries file.
u startup_stm32f4xx.s
u system_stm32f4xx.c
n RHF407 Demo.uvproj and other project file
l Output: compile output file storage directory Finally project needed files are：

Attention should be paid that, when the processor is working with the highest rated frequency 168MHz, it may be hard to reach CAN baud rate. To avoid too much performance reduction, it is suggested to adopt 160MHz. All the peripheral are in low speed, so the frequency do not need to be too high, but fractional frequency could be set larger. Alter file system_stm32f4xx.c.

To start hardware floating point unit, macro definition should be also added at C/C++page for the project.
l USE_STDPERIPH_DRIVER
l STM32F4XX
l __FPU_PRESENT = 1
l __FPU_USED = 1
l ARM_MATH_CM4

## 4.2.3 Key file description

Realization of each drive program has been explained in previous basic routine, but only the frame is different. CAN bus driver is different, especially for baud rate and acceptance filter. Baud rate could be set as 500Kbps, acceptance filter would accept all IDs’ surround, rather than select as before. Now introduction of other files:

### 4.2.3.1 app_main.c

Program subject. User control code start from main function.

// Name: main; // Function: C main function; // parameter: none; // return： none; // explaination: none; int main( void ); app_main_system_init();; while ( 1 ); if( drv_button_get_status(Button2) ); // recheck button status drv_delay_ms(200);; continue;; //parameter error, LED3 light on; drv_led_on(LED3);

//=========================================================================

//=========================================================================

if( 0 == drv_button_get_status(Button2) )

// if press buttion 2,move in a straight line, clockwise, 02m/s, 0 direction, rectangle, length of sides 08m and 1.6m separately if( app_robot_control_move_rectangle(1, 0.2, 0, 0.8, 1.6) )

else
{
drv_led_off(LED3);
}
}

if( drv_button_get_status(Button3) ) {
// recheck button status
drv_delay_ms(200);
if( 0 == drv_button_get_status(Button3) ) {
continue;
}
// if press buttion3, rotate movement, linear speed of wheel 0.2m/s, rotate time 20s
if( app_robot_control_move_rotate(0.2, 20000) )
{
// parameter error, LED3 light on drv_led_on(LED3);
}
else
{
drv_led_off(LED3);
}
}
}
}
Enter into main circulation status after initialization, check button status during circulation. Select different buttons according to aimed movement. call initialization programs of each driver in system initialization function app_main_system_init. //========================================================================= ===
// name: app_main_system_init
// function: system initialization
// parameter: none
// return: none
// explain: none

//========================================================================= ===
void app_main_system_init( void )
{
drv_led_init();
drv_button_init(); // notice key initialization in query mode drv_delay_init();
drv_can_init();
drv_uart_init(UART_BAUDRATE_9600);
}

### 4.2.3.2 app_robot_control.c

This file could realize chassis control action. Header file shall be included at the top for calculation will use sine and cosine function in the DSP function library. #include "arm_math.h"
Use the macro selective control command sending mode, serial port or CAN bus // send command from UART, send command from CAN aferannotation
#define SEND_MSG_FROM_UART | 1

define motor driver device type and device address
// define platform motor driver address
#define MOTOR_DIRVER_ADDRESS | 0x51 // configure in

accordance with platform manual
// define motor driver device type and device address
#define MOTOR_DRIVER_DEVICE_TYPE | 0x40

radian unit is adopted ain angle calculation, in consideration of multiplication is faster than division operation, so add several constants’ macro defination
// define floating-point calculation constant
#define PI_DIV2 | (PI / 2)

#define PI_DIV180 | (PI / 180)

#define _180_DIV_PI | (180 / PI)

The platform will finally stop whatever the movement mode is.realize stop movement function, write function //========================================================================= ===
// name: app_robot_control_move_abort
// function: control robot to stop
// parameter: none

// return: none
// description: set all the motors’ speed to be 0 //========================================================================= ===
void app_robot_control_move_abort( void )
{
INT8U ZeroSpeed[8] = { 0, 0, 0, 0, 0, 0, 0, 0 };

#ifdef SEND_MSG_FROM_UART

app_protocol_uart_send_msg(MOTOR_DRIVER_DEVICE_TYPE, MOTOR_DIRVER_ADDRESS, UARTCMD_SetMotorSpeed, ZeroSpeed, 8 ); #else
app_protocol_can_send_package(MOTOR_DIRVER_ADDRESS, CANCMD_SetMotorSpeed, 0, ZeroSpeed, 8);
#endif

drv_delay_ms(500);
}
Send command to make all the speed of motors to be 0.through previously defined macro control from serial port CAN send command.
Write the first movement function to be realized rectangle and diagonal movement. For flexible control, it is suggest setting start direction. Set move linear speed, side lengths of rectangle and movement locus to be clockwise or anti-clockwise direction. This movement locus is formed by 8 tangential paths. Take anti-clockwise locus for example, see drawing below:

Command control could only control platform’s move speed. Move time of each section could be controlled to control distance. Sudden turn will have applied force on part of motor. To avoid this, add delayer after stop of each movement. //========================================================================= ===
// name: app_robot_control_move_rectangle
// function: control platform to realize retangel command.
// parameter：RouteDir：locus，1 means anti-clockwise direction，0 means clockwise direction
// Speed: straight line movement speed, unit m/s, nonnegative number
// StartDir：initial move direction, -180°~180°
// Len1：length of first side for movement，unit m，positive number
// Len2：length of second side for movement，unit m，positive number
// return: none
// description: can not rotate, rectangle movement then turnback by diagonal movement //========================================================================= ===
INT8U app_robot_control_move_rectangle( INT8U RouteDir, float Speed,
float StartDir, float Len1, float Len2 ) {
LineMoveDataType LineCmdBuffer[8]; // restore command parameters of 4 sides of rectangle and diagonal movement
INT32U | DelayMs[8]; | // | restore | delayer | of each
movement
float StartDirRad; | // radian value of start direction
float SecondLineDirRad; | // radian value of the second line of

rectangle
float DiagonalRad; | // radian value of diagonal
float DiagonalLength; | // length of diagonal
INT8U i;

// check validity of parameters

// calculate radian angle and length of diagonal StartDirRad = StartDir * PI_DIV180;
DiagonalRad = atan2(Len2, Len1);
DiagonalLength = abs(Len2 / arm_sin_f32(DiagonalRad));

// calculate the first line
LineCmdBuffer[0].SpeedX = (INT16S)(Speed * arm_cos_f32(StartDirRad) * 10000); LineCmdBuffer[0].SpeedY = (INT16S)(Speed * arm_sin_f32(StartDirRad) * 10000); LineCmdBuffer[0].SpeedRotate = 0;
LineCmdBuffer[0].Acceleration = 0;
DelayMs[0] = ( INT32U )(Len1 * 1000 / Speed);

// calculate the second line
// judge angle viaration according to length value symbol if( RouteDir )
{
SecondLineDirRad = StartDirRad + PI_DIV2;
}
else
{
SecondLineDirRad = StartDirRad - PI_DIV2;
}
LineCmdBuffer[1].SpeedX = (INT16S)(Speed * arm_cos_f32(SecondLineDirRad) * 10000);
LineCmdBuffer[1].SpeedY = (INT16S)(Speed * arm_sin_f32(SecondLineDirRad) * 10000); LineCmdBuffer[1].SpeedRotate = 0;
LineCmdBuffer[1].Acceleration = 0;
DelayMs[1] = ( INT32U )(Len2 * 1000 / Speed);

// speed of the third line and first line in reverse,same time

// speed of the third line and first line in reverse,same time

// diagonal line starting from original point
if( RouteDir )
{
SecondLineDirRad = StartDirRad + DiagonalRad; }
else
{
SecondLineDirRad = StartDirRad - DiagonalRad;
}
LineCmdBuffer[4].SpeedX = (INT16S)(Speed * arm_cos_f32(SecondLineDirRad) * 10000);
LineCmdBuffer[4].SpeedY = (INT16S)(Speed * arm_sin_f32(SecondLineDirRad) * 10000); LineCmdBuffer[4].SpeedRotate = 0;
LineCmdBuffer[4].Acceleration = 0;
DelayMs[4] = ( INT32U )(DiagonalLength * 1000 / Speed);

// copy the third straight line

// operate another diagonal route
if( RouteDir )
{
SecondLineDirRad = StartDirRad - DiagonalRad; }
else
{
SecondLineDirRad = StartDirRad + DiagonalRad;
}
LineCmdBuffer[6].SpeedX = (INT16S)(Speed * arm_cos_f32(SecondLineDirRad) * 10000);
LineCmdBuffer[6].SpeedY = (INT16S)(Speed * arm_sin_f32(SecondLineDirRad) * 10000); LineCmdBuffer[6].SpeedRotate = 0;
LineCmdBuffer[6].Acceleration = 0;
DelayMs[6] = DelayMs[4];

for( i = 0; i < 8; i++ ); #ifdef SEND_MSG_FROM_UART; #else; CANCMD_SetPlatformSpeed,; 0, (INT8U *)(&LineCmdBuffer[i]), 8);; #endif; drv_delay_ms(DelayMs[i]);; app_robot_control_move_abort();; return ( 0 );

// operate theirst line in reverse direction, samewith the third parammeter

// send commands one by one to complete planed routine

app_protocol_uart_send_msg(MOTOR_DRIVER_DEVICE_TYPE,MOTOR_DIRVER_ADDRESS, UARTCMD_SetPlatformSpeed, (INT8U *)(&LineCmdBuffer[i]),

app_protocol_can_send_package(MOTOR_DIRVER_ADDRESS,

To complete 8 tangential paths, define an array to reserve speed parameters of 8 commands and define the processing time of the array reserving each command. Send in a sequence after calculating all the movements with delayers between each. Confirm a rectangle according to parameters input, calculate the angle between diagonal and the first line, and calculate length of diagonal according to the angle and line length. In this way it could improve efficiency for narrowed calculation range.
The two functions used above are arm_cos_f32 and arm_sin_f32, which originates from arm_cos_f32 and arm_sin_f32, and their calculation efficiency is higher than that in MDK library.
Some line parameters that are same or reversed are here neglected.
The second movement to be realized is rotation in stubby using set motor speed command; distance from wheel to rotation center of chassis could be used to calculate rotate angular speed. The speeds of all the wheels are the same and wheels will not move. This is user-friendly for starter. Combinations of different motor speeds will create complex movements. //========================================================================= ===
// name：app_robot_control_move_rotate
// function：control robot rotate
// parameter：UsrSpeed：user –defined speed, unit m/s

// MoveTimeMs： time of movement Ms
// return: none
// description: user-defined speed //========================================================================= ===
INT8U app_robot_control_move_rotate( float UsrSpeed, INT32U MoveTimeMs )
{
INT8U SpeedDataBuffer[8];
INT16S tmpSpeed;

if( UsrSpeed <= 0 )
{
return 1;
}

if( MoveTimeMs <= 0 )
{
return 2;
}

tmpSpeed = (INT16S)(UsrSpeed * 10000); // Linear speed of wheels needs to be mutitiplied by 1000 for transmission SpeedDataBuffer[0] = tmpSpeed & 0xFF;
SpeedDataBuffer[1] = tmpSpeed >> 8;
SpeedDataBuffer[2] = SpeedDataBuffer[0]; SpeedDataBuffer[3] = SpeedDataBuffer[1]; SpeedDataBuffer[4] = SpeedDataBuffer[0]; SpeedDataBuffer[5] = SpeedDataBuffer[1]; SpeedDataBuffer[6] = SpeedDataBuffer[0]; SpeedDataBuffer[7] = SpeedDataBuffer[1];

#ifdef SEND_MSG_FROM_UART

app_protocol_uart_send_msg( | MOTOR_DRIVER_DEVICE_TYPE,
MOTOR_DIRVER_ADDRESS,
UARTCMD_SetMotorSpeed, SpeedDataBuffer, 8 ); #else
app_protocol_can_send_package(MOTOR_DIRVER_ADDRESS, CANCMD_SetMotorSpeed,

0, SpeedDataBuffer, 8);
#endif

drv_delay_ms(MoveTimeMs);
app_robot_control_move_abort();

return ( 0 );
}

### 4.2.3.3 app_protocol_can.c

CAN protocol processing file. When receiving a CAN data package in CAN interrupt receiving service program, call app_protocol_can_msg_process in this file to process CAN message.
//========================================================================= ===
// name：app_protocol_can_msg_process
// function:CAN message process
// parameter:none
// return: none
// description:none
//========================================================================= ===
void app_protocol_can_msg_process( CanRxMsg RxMsg )
{
CanCommandType l_CanCmd;

l_CanCmd.CmdAddress = app_protocol_can_extid_get_address(RxMsg.ExtId); l_CanCmd.CmdFunc = app_protocol_can_extid_get_funcode(RxMsg.ExtId); l_CanCmd.CmdIndex = app_protocol_can_extid_get_index(RxMsg.ExtId); l_CanCmd.pData = RxMsg.Data;
l_CanCmd.MsgLen = RxMsg.DLC;

app_protocol_can_protocol_parse(l_CanCmd.CmdFunc,l_CanCmd.CmdIndex,l_CanCmd.pData); }
app_protocol_can_extid_get_address extract device address information from message ID. app_protocol_can_extid_get_funcode extract command, app_protocol_can_extid_get_index extract subcommand. Their macro definition as

follows:
#define app_protocol_can_extid_get_index(ID) | ((INT8U)((ID & 0X00FF0000) >> 16))

#define app_protocol_can_extid_get_funcode(ID) | ((INT8U)((ID & 0X0000FF00) >> 8))

#define app_protocol_can_extid_get_address(ID) | ((INT8U)(ID & 0X000000FF))

After extracting information from message process function, call app_protocol_can_protocol_parse to command prasing and execute commond. //========================================================================= ===
// name:app_protocol_can_protocol_parse
// function:CAN protocol prasing
// parameter:Cmd：function code
// | Index：index, subcommand
// | Msg：data
// return：0 means success, others mean fail
// description: none
//========================================================================= ===
INT8U app_protocol_can_protocol_parse( INT8U Cmd, INT8U Index, INT8U *Data )
{
switch ( Cmd )
{
case CANCMD_SetMotorSpeed: | // user defined motor speed
{
}
break;
case CANCMD_SetPlatformSpeed: // user defined platform speed {
}
break;
default:
{
return ( 1 );
}
}
return ( 0 );
}
This is just a program frame, no process to the message returned by moter driver.

As for protocol layer, it is important to send packaging of data package according to the protocol. The code as follows: //========================================================================= ===
// name:app_protocol_can_send_package
// function: send data package through CAN
// parameter:Address：adress
// | Cmd：function code
// | Index：functional code subpackage transmission index
// | Data：data
// | Len：length of data
// return: none
// description: none
//========================================================================= ===
INT8U app_protocol_can_send_package( INT8U Address, INT8U Cmd, INT8U Index,
| INT8U *Data, INT8U Len )
{
| CanTxMsg l_CanTxMsg;
| l_CanTxMsg.ExtId = app_protocol_can_extid_set(Index, Cmd, Address);
| l_CanTxMsg.StdId = 0;
| l_CanTxMsg.DLC = Len;
| l_CanTxMsg.RTR = CAN_RTR_DATA;
| l_CanTxMsg.IDE = CAN_ID_EXT;
| if( Len > 0 )
{
| INT8U i;
| for( i = 0; i < Len; i++ )
| {
| l_CanTxMsg.Data[i] = Data[i];
| }
}
| drv_can_send_msg(l_CanTxMsg);

return ( 0 );
}
app_protocol_can_extid_set is used for settle address, command and subcommandinto message ID. The macro definition is as follows: #define app_protocol_can_extid_set(index, cmd, address) \
((INT32U)((index<<16) | (cmd<<8) | address))
Call drv_can_send_msg function in drive layer to send out message.

### 4.2.3.4 app_protocol_uart.c

Serial protocol process file. There is no message processed from serial port, just send out message in form of packaging in accordance with protocol. //========================================================================= ===
// name:app_protocol_uart_send_msg
// function:serial port send fuction
// parameter:DeviceType
// | Address
// | DeviceId：device ID
// | Cmd：data package command code
// | Len：valid data length, one byte
// | Dat：valid data
// return: none
// description: continuously send when transmission, can not suspend, long time suspend willlead receivers to recognize end of transmission. //========================================================================= ===
void app_protocol_uart_send_msg( INT8U DeviceType, INT8U Address,
INT8U Cmd, INT8U *Dat, INT8U Len ) {
INT8U | SendBuffer[100];
INT8U | i = 0, j;
INT16U Crc16Value;

SendBuffer[i++] = UART_MSG_PACKAGE_STARTCHAR; SendBuffer[i++] = DeviceType;
SendBuffer[i++] = Address;
SendBuffer[i++] = Cmd;
SendBuffer[i++] = Len;

for( j = 0; j < Len; j++ )
{
SendBuffer[i++] = Dat[j];
}
Crc16Value = app_protocol_uart_crc16(SendBuffer, i); SendBuffer[i++] = ( INT8U )Crc16Value; SendBuffer[i++] = ( INT8U )(Crc16Value >> 8);
SendBuffer[i++] = UART_MSG_PACKAGE_ENDCHAR;

// send out data in buffer area in form ofblocking from serial port drv_uart_put_multi_bytes_blocking(SendBuffer, i);
}
Assign variate accordingly for buffer area in function, calculate CRC check value, then attach end mark, continuously send. Calculate CRC check code as follows: const INT16U crc_ta[256] = { /* CRC余式表 */
0x0000, 0x1021, 0x2042, 0x3063, 0x4084, 0x50a5, 0x60c6, 0x70e7,
0x8108, 0x9129, 0xa14a, 0xb16b, 0xc18c, 0xd1ad, 0xe1ce, 0xf1ef, 0x1231, 0x0210, 0x3273, 0x2252, 0x52b5, 0x4294, 0x72f7, 0x62d6, 0x9339, 0x8318, 0xb37b, 0xa35a, 0xd3bd, 0xc39c, 0xf3ff, 0xe3de, 0x2462, 0x3443, 0x0420, 0x1401, 0x64e6, 0x74c7, 0x44a4, 0x5485, 0xa56a, 0xb54b, 0x8528, 0x9509, 0xe5ee, 0xf5cf, 0xc5ac, 0xd58d, 0x3653, 0x2672, 0x1611, 0x0630, 0x76d7, 0x66f6, 0x5695, 0x46b4, 0xb75b, 0xa77a, 0x9719, 0x8738, 0xf7df, 0xe7fe, 0xd79d, 0xc7bc, 0x48c4, 0x58e5, 0x6886, 0x78a7, 0x0840, 0x1861, 0x2802, 0x3823, 0xc9cc, 0xd9ed, 0xe98e, 0xf9af, 0x8948, 0x9969, 0xa90a, 0xb92b, 0x5af5, 0x4ad4, 0x7ab7, 0x6a96, 0x1a71, 0x0a50, 0x3a33, 0x2a12, 0xdbfd, 0xcbdc, 0xfbbf, 0xeb9e, 0x9b79, 0x8b58, 0xbb3b, 0xab1a, 0x6ca6, 0x7c87, 0x4ce4, 0x5cc5, 0x2c22, 0x3c03, 0x0c60, 0x1c41, 0xedae, 0xfd8f, 0xcdec, 0xddcd, 0xad2a, 0xbd0b, 0x8d68, 0x9d49, 0x7e97, 0x6eb6, 0x5ed5, 0x4ef4, 0x3e13, 0x2e32, 0x1e51, 0x0e70, 0xff9f, 0xefbe, 0xdfdd, 0xcffc, 0xbf1b, 0xaf3a, 0x9f59, 0x8f78, 0x9188, 0x81a9, 0xb1ca, 0xa1eb, 0xd10c, 0xc12d, 0xf14e, 0xe16f, 0x1080, 0x00a1, 0x30c2, 0x20e3, 0x5004, 0x4025, 0x7046, 0x6067, 0x83b9, 0x9398, 0xa3fb, 0xb3da, 0xc33d, 0xd31c, 0xe37f, 0xf35e, 0x02b1, 0x1290, 0x22f3, 0x32d2, 0x4235, 0x5214, 0x6277, 0x7256,

0xb5ea, 0xa5cb, 0x95a8, 0x8589, 0xf56e, 0xe54f, 0xd52c, 0xc50d, 0x34e2, 0x24c3, 0x14a0, 0x0481, 0x7466, 0x6447, 0x5424, 0x4405, 0xa7db, 0xb7fa, 0x8799, 0x97b8, 0xe75f, 0xf77e, 0xc71d, 0xd73c, 0x26d3, 0x36f2, 0x0691, 0x16b0, 0x6657, 0x7676, 0x4615, 0x5634, 0xd94c, 0xc96d, 0xf90e, 0xe92f, 0x99c8, 0x89e9, 0xb98a, 0xa9ab, 0x5844, 0x4865, 0x7806, 0x6827, 0x18c0, 0x08e1, 0x3882, 0x28a3, 0xcb7d, 0xdb5c, 0xeb3f, 0xfb1e, 0x8bf9, 0x9bd8, 0xabbb, 0xbb9a, 0x4a75, 0x5a54, 0x6a37, 0x7a16, 0x0af1, 0x1ad0, 0x2ab3, 0x3a92, 0xfd2e, 0xed0f, 0xdd6c, 0xcd4d, 0xbdaa, 0xad8b, 0x9de8, 0x8dc9, 0x7c26, 0x6c07, 0x5c64, 0x4c45, 0x3ca2, 0x2c83, 0x1ce0, 0x0cc1, 0xef1f, 0xff3e, 0xcf5d, 0xdf7c, 0xaf9b, 0xbfba, 0x8fd9, 0x9ff8, 0x6e17, 0x7e36, 0x4e55, 0x5e74, 0x2e93, 0x3eb2, 0x0ed1, 0x1ef0
};

//========================================================================= ===
// name: app_protocol_uart_crc16
// function: calculate checksum
// parameter: *ptr：caculate charater string of checksum // len：length of bytes
// return: none
// description: none
//========================================================================= ===
static INT16U app_protocol_uart_crc16( INT8U *ptr, INT16U len )
{
| INT16U crc; INT8U da; crc = 0; while ( len-- != 0 )

{
| da = ( INT8U )(crc >> 8); crc <<= 8; crc ^= crc_ta[da ^ *ptr]; ptr++;

}
| return ( crc );

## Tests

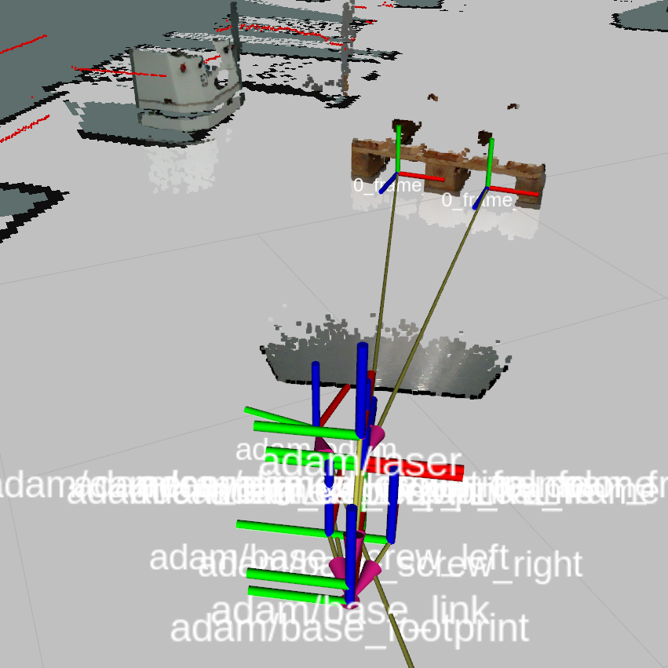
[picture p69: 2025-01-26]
docs/assets/preprint/figs/results_pallet-detection.png

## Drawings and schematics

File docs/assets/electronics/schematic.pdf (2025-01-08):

+

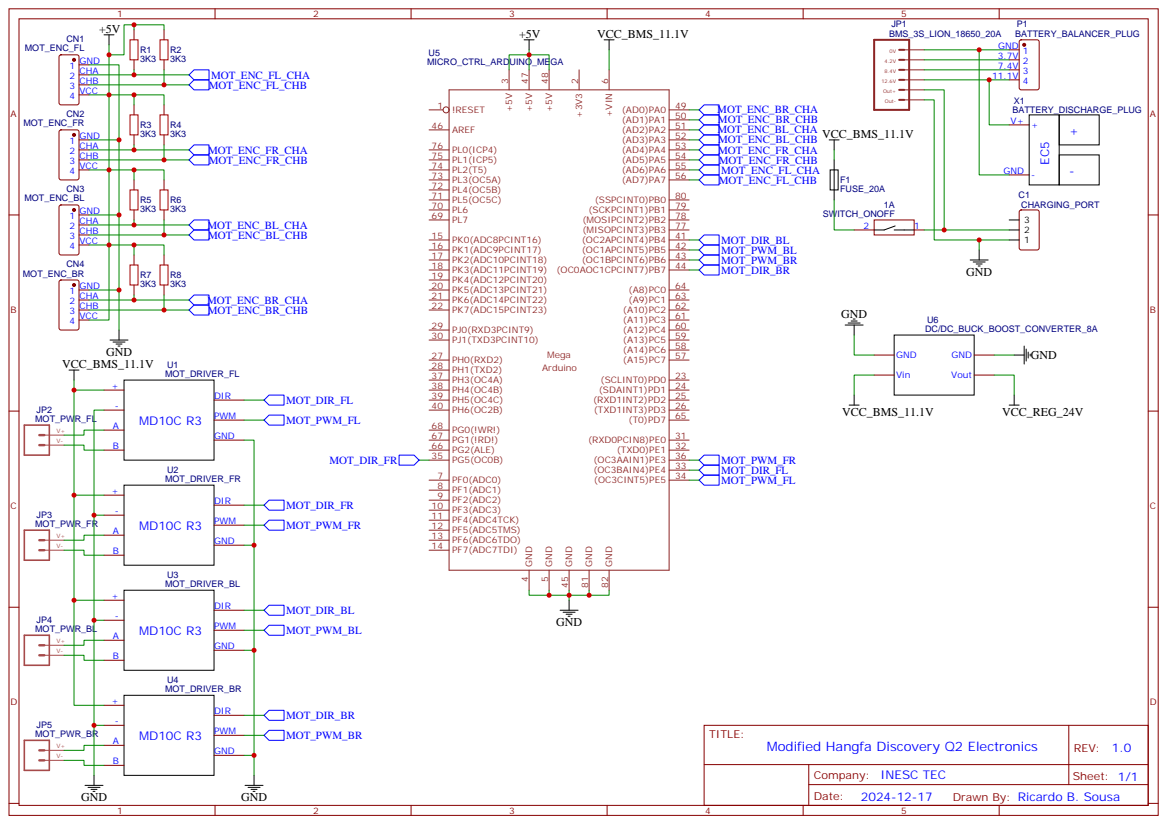
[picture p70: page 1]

Drawn By: Ricardo B. Sousa

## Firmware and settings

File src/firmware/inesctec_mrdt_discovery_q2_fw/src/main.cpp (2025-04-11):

#include <Arduino.h>
#include <channels.h>

#include "Robot.h"

/******************************************************************************
 * GLOBAL VARIABLES
 ******************************************************************************/
unsigned long current_micros = 0, previous_micros = 0;
unsigned long last_motor_update_millis = 0;
bool timeout = false;
channels_t serial_channels;
// uint8_t builtin_led_state;

Robot robot;
Encoder* encoders = robot.enc;

/******************************************************************************
 * FUNCTIONS HEADERS
 ******************************************************************************/
void processSerialPacket(char channel, uint32_t value, channels_t& obj);
void serialWrite(uint8_t b);
void serialWriteChannel(char channel, int32_t value);
void serialRead();
void checkMotorsTimeout();

/******************************************************************************
 * IMPLEMENTATION
 ******************************************************************************/
void setup()
{
  // Built-in LED
  // NOT IN USE: same pin as BR_DIR!!!!!
  /*builtin_led_state = LOW;
  pinMode(LED_BUILTIN, OUTPUT);
  digitalWrite(LED_BUILTIN, builtin_led_state);*/

  // Robot
  robot.init(serialWriteChannel);

  // Serial communication
  Serial.begin(115200);
  serial_channels.init(processSerialPacket, serialWrite);

  // Reset signal
  serialWriteChannel('r', 0);

  // Test PWM motors
  /*robot.setMotorPWM(0, 0);
  robot.setMotorPWM(1, 0);
  robot.setMotorPWM(2, 0);
  robot.setMotorPWM(3, 0);*/

  // Initialization
  current_micros = micros();
  previous_micros = current_micros;
  last_motor_update_millis = millis();
}

void loop()
{
  // static unsigned long blink_led_decimate = 0;
  uint32_t delta;

  serialRead();

  current_micros = micros();
  delta = current_micros - previous_micros;
  if (delta > kMotCtrlTimeUs)
  {
    if (kMotCtrlTimeoutEnable)
    {
      checkMotorsTimeout();
    }

    if (!timeout)
    {
      previous_micros = current_micros;

      // Update and send data
      robot.update(delta);
      robot.send();

      // Debug (Serial Monitor)
      // serialWrite('\n');

      // Blink LED
      /*blink_led_decimate++;
      if (blink_led_decimate >= kMotCtrlLEDOkCount) {
        if (builtin_led_state == LOW) {
          builtin_led_state = HIGH;
        } else {
          builtin_led_state = LOW;
        }
        digitalWrite(LED_BUILTIN, builtin_led_state);
        blink_led_decimate = 0;
      }*/
    }
  }
}

/******************************************************************************
 * FUNCTIONS IMPLEMENTATIONS
 ******************************************************************************/
void processSerialPacket(char channel, uint32_t value, channels_t& obj)
{
  uint8_t mot_i;
  int16_t pwm;

  // Reset watchdog
  if ((channel == 'G') || (channel == 'K'))
  {
    last_motor_update_millis = millis();
  }

  // Process incomming serial packet
  switch (channel)
  {
    // - reference angular speed
    case 'G':
    case 'H':
    case 'I':
    case 'J':
      mot_i = channel - 'G';
      // set reference angular speed for the motors
#ifdef CONFIG_LAZARUS
      robot.setMotorWref(mot_i, ((int32_t) value) * kEncImp2MotW);
#endif
#ifdef CONFIG_ROS
      robot.setMotorWref(mot_i, *((float*) &value));
#endif
      break;

    // - PWM
    case 'K':
      mot_i = (value >> 24) & 0x03;
      pwm = value & 0xFFFF;
      robot.setMotorPWM(mot_i, pwm);
      break;
  }
}

void serialWrite(uint8_t b) { Serial.write(b); }

void serialWriteChannel(char channel, int32_t value)
{
  serial_channels.send(channel, value);
}

void serialRead()
{
  uint8_t serial_byte;

  if (Serial.available() > 0)
  {
    serial_byte = Serial.read();
    serial_channels.StateMachine(serial_byte);
  }
}

void checkMotorsTimeout()
{
  if (millis() - last_motor_update_millis > kMotCtrlTimeout)
  {
    timeout = true;

    robot.stop();

    /*builtin_led_state = LOW;
    digitalWrite(LED_BUILTIN, builtin_led_state);*/
  }
  else
  {
    if (timeout)
    {
      robot.init(serialWriteChannel);
    }

    timeout = 0;
  }
}

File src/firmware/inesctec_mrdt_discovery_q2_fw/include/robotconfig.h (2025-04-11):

#pragma once

#include <Arduino.h>
#include <TimerOne.h>
#include <TimerThree.h>

/******************************************************************************
 * Configuration (uncomment the appropriate configuration)
 * - Lazarus-based applications (original channels implementation)
 * - ROS-based navigation stack (modified implementation of channels with the
 *     using the ROS package serial_communication_channels
 ******************************************************************************/
// #define CONFIG_LAZARUS        //!< firmware communicates to a Lazarus app
#define CONFIG_ROS  //!< firmware communicates to a ROS-based app

/******************************************************************************
 * Robot parameters
 * - kinematic configuration
 * - battery
 ******************************************************************************/
const float kRobotL[] = {
    //!< robot geometric distances
    0.268,  //!< front-back wheel distance
    0.268   //!< left-right wheel distance
};
const float kRobotWhD[] = {
    //!< diameter of the wheels 0-3 (m)
    0.1016,  //!< back-right wheel
    0.1016,  //!< back-left  wheel
    0.1016,  //!< front-right wheel
    0.1016   //!< front-left  wheel
};
const float kRobotBattVnom = 11.1;  //!< nominal battery level (V)

/******************************************************************************
 * Motor parameters
 * - gear reduction ratio and encoders resolution
 * - controllers parameters
 ******************************************************************************/
const float kMotNgear = 64;       //!< gear reduction ratio (n:1)
const float kMotEncRes = 12 * 4;  //!< encoder resolution (tick count per rev.)

const uint8_t kMotEncPin0A = 22;  //!< encoder channel A of back-right wheel
const uint8_t kMotEncPin0B = 23;  //!< encoder channel B of back-right wheel
const uint8_t kMotEncPin1A = 24;  //!< encoder channel A of back-left wheel
const uint8_t kMotEncPin1B = 25;  //!< encoder channel B of back-left wheel
const uint8_t kMotEncPin2A = 26;  //!< encoder channel A of front-right wheel
const uint8_t kMotEncPin2B = 27;  //!< encoder channel B of front-right wheel
const uint8_t kMotEncPin3A = 28;  //!< encoder channel A of front-left wheel
const uint8_t kMotEncPin3B = 29;  //!< encoder channel B of front-left wheel

const int kMotDirPin[] = {
    13,  //!< back-right wheel
    10,  //!< back-left  wheel
    4,   //!< front-right wheel
    2    //!< front-left  wheel
};
const int kMotPwmPin[] = {
    TIMER1_B_PIN,  //!< back-right wheel
    TIMER1_A_PIN,  //!< back-left  wheel
    TIMER3_A_PIN,  //!< front-right wheel
    TIMER3_C_PIN   //!< front-left  wheel
};

const float kMotModelKp = 1.000;   //!< gain (rad.s^(-1) / V)
const float kMotModelTau = 0.100;  //!< time constant (s)
const float kMotModelLag = 0.000;  //!< lag lag (s)

const unsigned long kMotCtrlFreq = 100UL;       //!< frequency (Hz)
const float kMotCtrlTime = 1.0 / kMotCtrlFreq;  //!< period (s)
const unsigned long kMotCtrlTimeUs = 1000000UL / kMotCtrlFreq;
const unsigned long kMotCtrlTimeout = 100UL;  //!< watchdog timeout (ms)
const bool kMotCtrlTimeoutEnable = true;      //!< enable watchdog (true/false)

const unsigned long kMotCtrlLEDOkFreq = 4UL;  //!< heartbeat LED frequency (Hz)
const unsigned long kMotCtrlLEDOkCount =
    1000000UL / kMotCtrlLEDOkFreq / kMotCtrlTimeUs / 2;

const float kMotVmax = 12;        //!< maximum voltage appliable to motors (V)
const int16_t kMotPWMmax = 1023;  //!< maximum PWM (0..1023)
const int16_t kMotPWMDeltaMax = 150;  //!< maximum variation in PWM (0..1023)
const bool kMotPWMDeltaMaxEnabled = true;  //!< enable limits on PWM variation

const float kMotHammV0 = 0;  //!< estimated motors' deadzone (V)
const float kMotHammVd = 0;  //!< compensated motors' deadzone (V)

//! IMC tunning: desired time constant for the closed-loop (s)
const float kMotCtrlTauCl = kMotModelTau / 1.5;
//! IMC tunning: Kc_PI * Kp_plant
const float kMotCtrlKcKp = kMotModelTau / (kMotCtrlTauCl + kMotModelLag);
//! PI proportional gain (V / rad.s^(-1))
const float kMotCtrlKc = kMotCtrlKcKp / kMotModelKp;
//! PI integration time (s)
const float kMotCtrlTi = kMotModelTau;

/******************************************************************************
 * Conversion constants
 ******************************************************************************/
//! Conversion constant: encoder pulses (ticks) > motor angular speed (rad/s)
const float kEncImp2MotW =
    2 * PI * 1000000 / (1.0 * kMotCtrlTimeUs * kMotNgear * kMotEncRes);
//! Conversion constant: motor voltage (V) > PWM (0..PWM_max)
const float kMotV2MotPWM = kMotPWMmax * 1.0 / kRobotBattVnom;

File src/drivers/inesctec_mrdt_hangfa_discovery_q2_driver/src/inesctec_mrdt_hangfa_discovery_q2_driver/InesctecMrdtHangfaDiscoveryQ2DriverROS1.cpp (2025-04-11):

#include "inesctec_mrdt_hangfa_discovery_q2_driver/InesctecMrdtHangfaDiscoveryQ2DriverROS1.h"

namespace inesctec_mrdt_hangfa_discovery_q2_driver
{

InesctecMrdtHangfaDiscoveryQ2DriverROS1::
    InesctecMrdtHangfaDiscoveryQ2DriverROS1()
    : nh_priv_("~"), serial_comms_first_fault_(true)
{
  try
  {
    getParam();
  }
  catch (std::exception &e)
  {
    ROS_FATAL("Error reading the node parameters (%s)", e.what());

    ros::shutdown();

    return;
  }

  sample_time_ = ros::Time::now();

  pub_mot_enc_ =
      nh_.advertise<inesctec_mrdt_drivers_interfaces::MotEncArrayROS1>(
          "motors_enc", 10);

  sub_mot_ref_ =
      nh_.subscribe<inesctec_mrdt_drivers_interfaces::MotRefArrayROS1>(
          "motors_ref", 1, &InesctecMrdtHangfaDiscoveryQ2DriverROS1::subMotRef,
          this);

  rob_.setSerialPortName(serial_port_name_);
  rob_.openSerial();

  rob_.run = std::bind(&InesctecMrdtHangfaDiscoveryQ2DriverROS1::run, this);
  rob_.init();

  serial_port_timer_ = nh_.createTimer(
      ros::Duration(1),
      boost::bind(&InesctecMrdtHangfaDiscoveryQ2DriverROS1::checkSerialComms,
                  this));
}

void InesctecMrdtHangfaDiscoveryQ2DriverROS1::getParam()
{
  nh_priv_.param("encoder_res", encoder_res_, 48.0);
  nh_priv_.param("gear_reduction", gear_reduction_, 64.0);
  nh_priv_.param<std::string>("serial_port_name", serial_port_name_,
                              "/dev/ttyACM0");

  for (auto &m : rob_.mot)
  {
    m.encoder_res = encoder_res_;

    m.gear_reduction = gear_reduction_;
  }

  ROS_INFO("[%s] Encoder resolution: %lf (ticks/rev)",
           ros::this_node::getName().c_str(), rob_.mot[0].encoder_res);

  ROS_INFO("[%s] Gear reduction ratio: %lf (n:1)",
           ros::this_node::getName().c_str(), rob_.mot[0].gear_reduction);

  ROS_INFO("[%s] Serial port: %s", ros::this_node::getName().c_str(),
           serial_port_name_.c_str());
}

void InesctecMrdtHangfaDiscoveryQ2DriverROS1::checkSerialComms()
{
  if (!rob_.isSerialOpen())
  {
    if (serial_comms_first_fault_)
    {
      serial_comms_first_fault_ = false;

      ROS_INFO(
          "[%s] Couldn't open the serial port %s. Will retry every second.",
          ros::this_node::getName().c_str(), serial_port_name_.c_str());
    }

    rob_.mtx_.lock();
    rob_.stopMotors();
    rob_.mtx_.unlock();

    rob_.closeSerial();
    rob_.openSerial();

    if (rob_.isSerialOpen())
    {
      serial_comms_first_fault_ = true;

      ROS_INFO("[%s] Opened serial port %s.", ros::this_node::getName().c_str(),
               serial_port_name_.c_str());

      rob_.init();
    }
  }
}

void InesctecMrdtHangfaDiscoveryQ2DriverROS1::run()
{
  try
  {
    if (ros::Duration(ros::Time::now() - sample_time_) >
        ros::Duration(kWatchdogMotWRef))
    {
      rob_.mtx_.lock();
      rob_.stopMotors();
      rob_.mtx_.unlock();
    }
  }
  catch (std::exception &e)
  {
    ROS_WARN("[%s] Not possible to check the driver timeout condition (%s)",
             ros::this_node::getName().c_str(), e.what());

    sample_time_ = ros::Time::now();

    return;
  }

  pubMotEnc();
}

void InesctecMrdtHangfaDiscoveryQ2DriverROS1::pubMotEnc()
{
  inesctec_mrdt_drivers_interfaces::MotEncArrayROS1 msg;

  msg.stamp = ros::Time::now();
  msg.mot_enc.resize(4);

  rob_.mtx_.lock();

  for (int i = 0; i < 4; i++)
  {
    msg.mot_enc[i].enc_delta = rob_.mot[i].getEncTicksDeltaPub();

    msg.mot_enc[i].ticks_per_rev =
        rob_.mot[i].encoder_res * rob_.mot[i].gear_reduction;

    msg.mot_enc[i].ang_speed = rob_.mot[i].w;
  }

  rob_.mtx_.unlock();

  pub_mot_enc_.publish(msg);
}

void InesctecMrdtHangfaDiscoveryQ2DriverROS1::subMotRef(
    const inesctec_mrdt_drivers_interfaces::MotRefArrayROS1::ConstPtr &msg)
{
  if (msg->ang_speed_ref.size() >= 4)
  {
    rob_.mtx_.lock();

    for (int i = 0; i < 4; i++)
    {
      rob_.mot[i].w_r = msg->ang_speed_ref[i].ref;
    }

    rob_.mtx_.unlock();

    sample_time_ = msg->stamp;
  }
}

}  // namespace inesctec_mrdt_hangfa_discovery_q2_driver

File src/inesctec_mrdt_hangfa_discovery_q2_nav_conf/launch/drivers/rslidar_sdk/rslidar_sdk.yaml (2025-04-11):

common:
  msg_source: 1                                         #0: not use Lidar
                                                        #1: packet message comes from online Lidar
                                                        #2: packet message comes from ROS or ROS2
                                                        #3: packet message comes from Pcap file
  send_packet_ros: false                                #true: Send packets through ROS or ROS2(Used to record packet)
  send_point_cloud_ros: true                            #true: Send point cloud through ROS or ROS2
lidar:
  - driver:
      lidar_type: RSHELIOS         #LiDAR type - RS16, RS32, RSBP, RSHELIOS, RSHELIOS_16P, RS128, RS80, RS48, RSP128, RSP80, RSP48, 
                                   #             RSM1, RSM1_JUMBO, RSM2, RSE1
      msop_port: 6699              #Msop port of lidar
      difop_port: 7788             #Difop port of lidar
      start_angle: 0               #Start angle of point cloud
      end_angle: 360               #End angle of point cloud 
      wait_for_difop: true
      min_distance: 0.55           #Minimum distance of point cloud
      max_distance: 150            #Maximum distance of point cloud
      use_lidar_clock: false       #True--Use the lidar clock as the message timestamp
                                   #False-- Use the system clock as the timestamp
      pcap_path: /home/robosense/lidar.pcap #The path of pcap file
    ros:
      ros_frame_id: lidar3d                            #Frame id of packet message and point cloud message
      ros_recv_packet_topic: lidar3d_packets           #Topic used to receive lidar packets from ROS
      ros_send_packet_topic: lidar3d_packets           #Topic used to send lidar packets through ROS
      ros_send_point_cloud_topic: lidar3d              #Topic used to send point cloud through ROS

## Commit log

2024-11-14 Hangfa Discovery Q2: platform manual + dimensions + motors datasheet
2024-11-14 sensors::lidar2d: hokuyo ust-10lx
    [hokuyo_ust-10lx_3d-model.STEP]
2024-11-14 sensors::lidar2d: ydlidar x4 (missing 3d model)
2024-11-14 sensors::lidar2d: ldrobot d300 ld19 (missing 3d model)
2024-11-14 sensors::lidar2d: slamtec rplidar s2 (missing 3d model)
2024-11-14 sensors::lidar2d: 3D models of LD19 + RPLIDAR S2 + X4
    [ldrobot_d300_ld19_3d-model.step, ydlidar_x4_3d-model.step]
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2024-11-14 sensors::lidar3d: robosense rs-helios-5515
    [robosense_rs-helios-5515_3d-model.STEP]
2024-11-14 sensors::lidar3d: velodyne vlp-16 (missing 3d model)
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2024-11-14 sensors::rgbd: intel realsense d455 + l515
    [intel_realsense_d455_3d-model.step]
2024-11-14 sensors::rgbd: luxonis oak-d pro
2024-11-17 models::v0 (old deprecated version): all Fusion models used for the first prototype modified version of Hanfga Dicovery Q2
    [battery_xiaomi-powerbank-20000mAh_box.f3d, electronics_baseplate.f3d, platform_hangfa-discovery-q2_draft.f3d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]
2024-11-22 models::v1: sensors bend plate 3D printed supports
    [sensors-plate_back-support_wi-fi-antennas.3mf, sensors-plate_back-support_wi-fi-antennas.f3d, sensors-plate_back-support_wi-fi-antennas.step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]
2024-11-23 models::v1: LiDAR 2D supports (UST-10LX, LD19, X4, and S2) for sensors bend plate
    [sensors-plate_lidar2d_hokuyo-ust-10lx_support.3mf, sensors-plate_lidar2d_hokuyo-ust-10lx_support.f3d, sensors-plate_lidar2d_hokuyo-ust-10lx_support.step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]
2024-11-23 models::v1: fix LD19 support
    [sensors-plate_lidar2d_ldrobot-d300-ld19_support.3mf, sensors-plate_lidar2d_ldrobot-d300-ld19_support.f3d, sensors-plate_lidar2d_ldrobot-d300-ld19_support.step]
2024-11-30 models::v1: Battery for Single Board Computer (SBC) - Xiaomi PowerBank 20.000mAh 50W
    [battery_xiaomi-powerbank-50W-20000mAh_case_bottom.3mf, battery_xiaomi-powerbank-50W-20000mAh_case_bottom.f3d, battery_xiaomi-powerbank-50W-20000mAh_case_bottom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]
2024-11-30 models::v1: Case for the Single Board Computer (SBC) LattePanda 3 Delta
    [sbc_lattepanda-3-delta_case.f3d, sbc_lattepanda-3-delta_case.step, sbc_lattepanda-3-delta_case_bottom.3mf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]
2024-12-03 models::v1: generic LiDAR 3D support (Velodyne VLP 16, Livox Mid 360, RS HELIOS 5515, Ouster)
    [sensors-plate_lidar3d_generic-support.3mf, sensors-plate_lidar3d_generic-support.f3d, sensors-plate_lidar3d_generic-support.step]
2024-12-07 sensors::imu: Xsens MTi-630 documentation + 3d model
2024-12-07 sensors::imu: Xsens MTi-630 fix documentation name + development kit user manual added
2024-12-07 sensors::imu: Xsens MTi-3 documentation + 3d models
    [xsens_mti-3-ahrs_3d-model_mti-1-series_v2.STEP, xsens_mti-3-ahrs_3d-model_mti-1-series_v2_dk-gnss.STEP, xsens_mti-3-ahrs_3d-model_mti-1-series_v3.STEP]
2024-12-08 models::v1: IMU Xsens MTi-630 support
    [sensors-plate_imu_xsens-mti-630-ahrs_case.f3d, sensors-plate_imu_xsens-mti-630-ahrs_case.step, sensors-plate_imu_xsens-mti-630-ahrs_case_bottom.3mf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]
2024-12-17 models::v1: OptiTrack markers support for the omni wheels (find the geometric / odometric centre of the robot)
    [hangfa-discovery-q2_optitrack_wheels-trackers_support.3mf, hangfa-discovery-q2_optitrack_wheels-trackers_support.f3d, hangfa-discovery-q2_optitrack_wheels-trac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]
2024-12-17 models::v1: electronics baseplate (to mount inside the Hangfa Discovery Q2 frame)
    [electronics_baseplate.f3d, electronics_baseplate.step, electronics_baseplate_base.3mf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]
2024-12-26 models::v1: OptiTrack markers for the sensors bend plate
    [hangfa-discovery-q2_optitrack_sensors-plate_trackers-support.f3d, hangfa-discovery-q2_optitrack_sensors-plate_trackers-support.step, hangfa-discovery-q2_optitr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]
2024-12-27 doc::electronics: initial version of electronics schematic (missing encoders external resistor)
2025-01-01 Initial version of the Bill Of Materials (BOM)
    [bom.xlsx]
2025-01-03 models::v1: IMU Xsens MTi-3 support
    [sensors-plate_imu_xsens-mti-3-ahrs_support.3mf, sensors-plate_imu_xsens-mti-3-ahrs_support.f3d, sensors-plate_imu_xsens-mti-3-ahrs_support.step]
2025-01-07 doc::electronics: add Hangfa Discovery Q2 encoders pinout + proto shield connections to repo
2025-01-08 doc::electronics: add PULLUP resistor required to count correctly the encoder's pulses
2025-01-08 doc::electronics: photos of the 3D framework to accomodate all electronics inside the robot
2025-01-16 sensors::lidar3d: fix missing documentation on specific Ouster (Ouster OS1 64 Rev C) and Velodyne (interface box)
2025-01-24 models::v1: update README - validation of the generic support with 3D LiDAR models
2025-01-24 models::v1: update README - validation of the front support of the bent metal sheet for RGBD cameras
2025-02-19 configure Material for MkDocs theme to generate GitHub PAge
2025-02-19 GitHub Action for Material for MkDocs
2025-02-23 GitHub Pages: Firmware Setup (STILL BUG on device specifics udev rules)
2025-02-23 GitHub Pages: reorganise electronics pages + add BOM page (still incomplete)
2025-02-24 update BOM (generate PDF with hyperlinks)
    [bom.xlsx]
2025-02-24 GitHub Pages: BOM (draft with embedded PDF)
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2025-02-24 Drivers::Serial Communication Channels library
2025-02-26 GitHub Pages: Electronics::Assembly guide (draft)
2025-02-26 GitHub Pages: Electronics::fix assembly links for arduino
2025-02-26 GitHub Pages: Electronics::add legend for the arduino mega proto shield images
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2025-02-26 GitHub Pages: SBC::Sigma add warning AX211 possibly missing drivers in Ubuntu 20
2025-02-27 GitHub Pages: complete power budgets with different possible ocnfigurations
2025-02-27 GitHub Pages: fix rated power drawn by Faulhaber OEM motors and consequently platform's autonomy
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2025-02-27 Reorganise sensor information into GitHub assets
    [hokuyo_ust-10lx_3d-model.STEP, intel_realsense_d455_3d-model.step, ldrobot_d300_ld19_3d-model.step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]
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2025-03-02 GitHub Pages: comparison table of LiDAR 3D and RGBD cameras
2025-03-02 GitHub Pages: comparison table of 2D laser scanners
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2025-04-10 Omnidirectional compatible joy driver
    [inesctec_mrdt_omnijoy_driver.cfg]
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2025-04-11 Formatting + update README on Hangfa Discovery Q2 driver
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2025-04-14 models::v1: Final model that includes all sensores and 3D parts into a single project
    [hangfa-discovery-q2_mechanical-platform.f3d, hangfa-discovery-q2_mechanical-platform.step]
